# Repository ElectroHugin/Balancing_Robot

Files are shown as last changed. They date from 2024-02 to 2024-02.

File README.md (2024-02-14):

# Balancing_Robot

## Description
Self balancing robot with two wheels. Scope of functionality depends on sensors and is still work in progress.

## Materials
- ESP32 Dev Kit C V4 mit CP2102
- Later on custom board with ESP32-S3-WROOM
- SiliconLabs Uart-to-USB CP2102
- ~~Accelerometer / Gyroscope / Magnetometer BNO085~~
- Accelerometer / Gyroscope MPU6050
- VL53L0X Time-of-Flight (TOF) Laser distance sensor
- (HC-SR04 Ultrasound Module)
- (MAX7219 8x8 1 Dot Matrix MCU LED Display Module)
- ~~BMP180 Barometric Air Pressure and Temperature Sensor~~
- ~~DHT22 Temperature Sensor and Humidity Sensor~~
- ~~Photo LDR Resistor Diodes~~
- ~~L298N H-Bridge Motor Driver~~
- TB6612FNG Motor Driver
- USB-C PD with Battery
- ~~MT3608 DC-DC power supply adapter step up module~~
    ~~- Input voltage: 2V - 24V~~
    ~~- Output voltage: 3V - 28V~~
- ~~OR M2596S Step-down DC-DC Buck Converter~~
    ~~-  Input voltage: 4-40V~~
    ~~-  Output voltage: 3.3-24V~~
- JGA25-371 DC-Motor 12V with Hall-Encoder 65mm wheels

## Visuals
### 3D Model

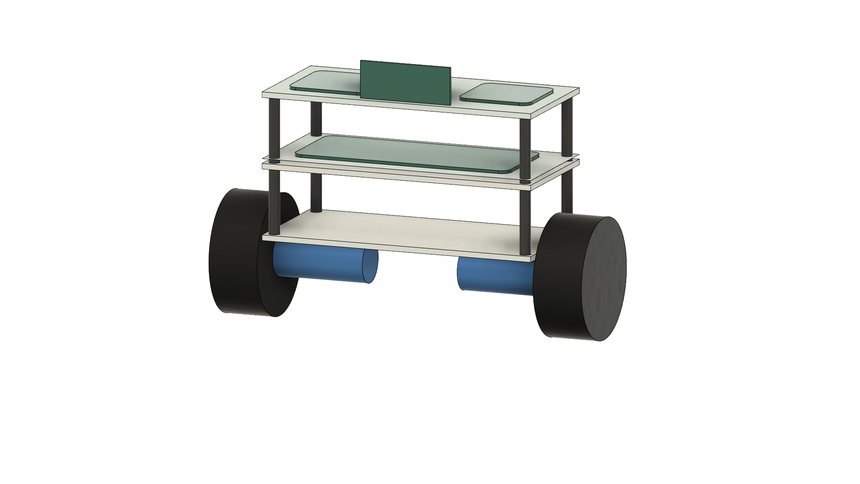
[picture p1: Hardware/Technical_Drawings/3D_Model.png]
Visual representation of 3D Model 3D-Render of Model


### PCB Models
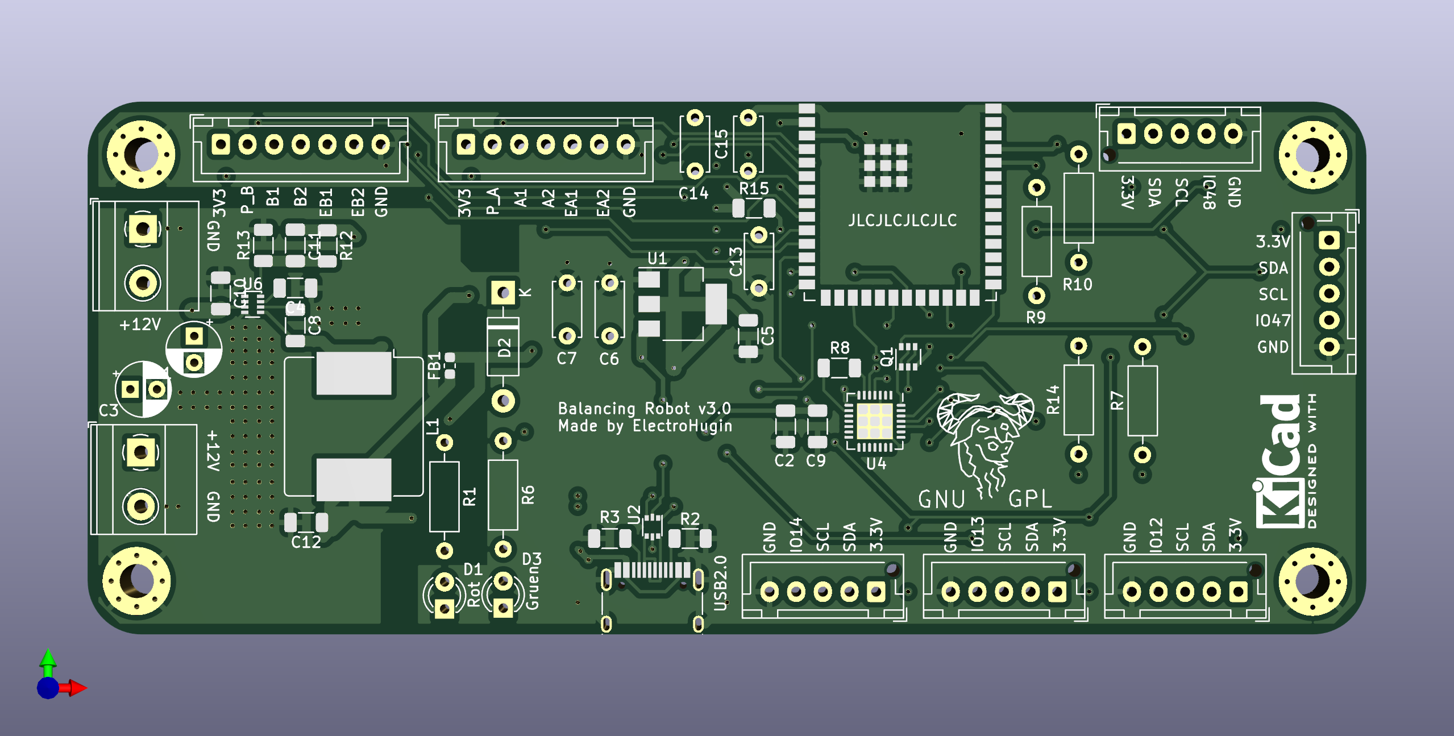
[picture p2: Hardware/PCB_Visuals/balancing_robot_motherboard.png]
Motherboard PCB of Motherboard


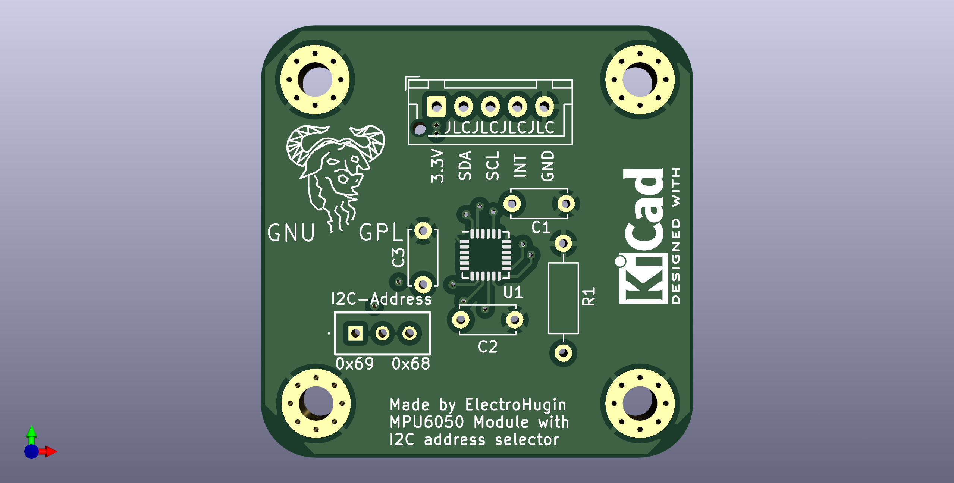
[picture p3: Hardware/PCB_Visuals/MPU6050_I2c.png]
MPU6050 PCB of MPU6050-Board


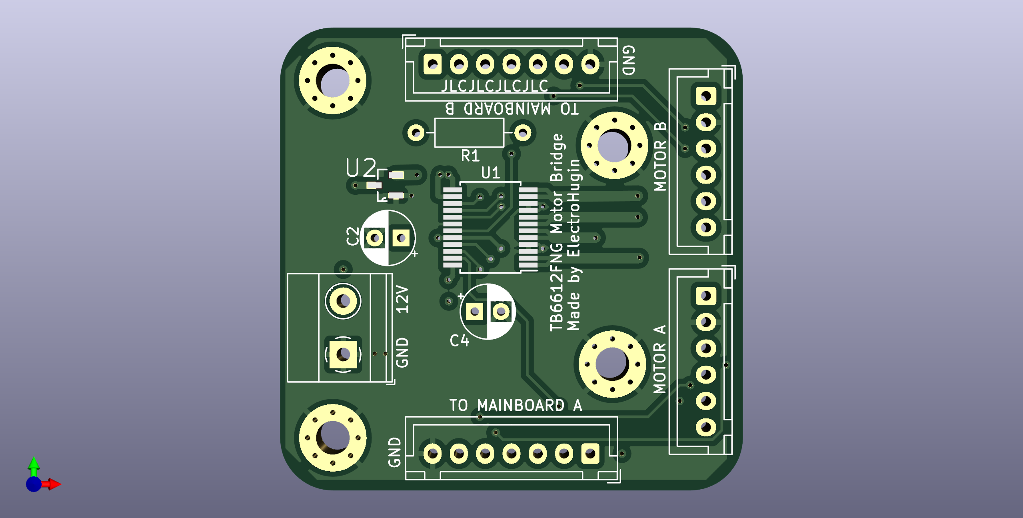
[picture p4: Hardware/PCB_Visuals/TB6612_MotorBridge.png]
Motherboard PCB of TB6612FNG-Board


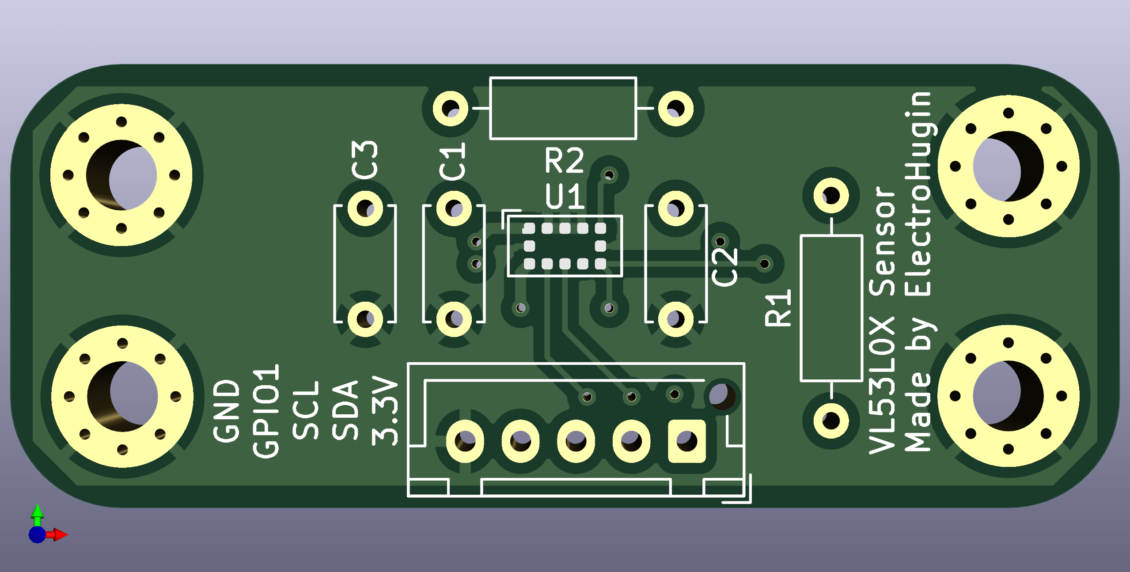
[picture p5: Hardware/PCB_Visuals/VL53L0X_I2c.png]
Motherboard PCB of VL53L0X-Board


## Installation
WIP

## Usage
WIP

## License
Licenses under GNU GENERAL PUBLIC LICENSE Version 3, 29 June 2007

## Project status
Still at the beginning of project.

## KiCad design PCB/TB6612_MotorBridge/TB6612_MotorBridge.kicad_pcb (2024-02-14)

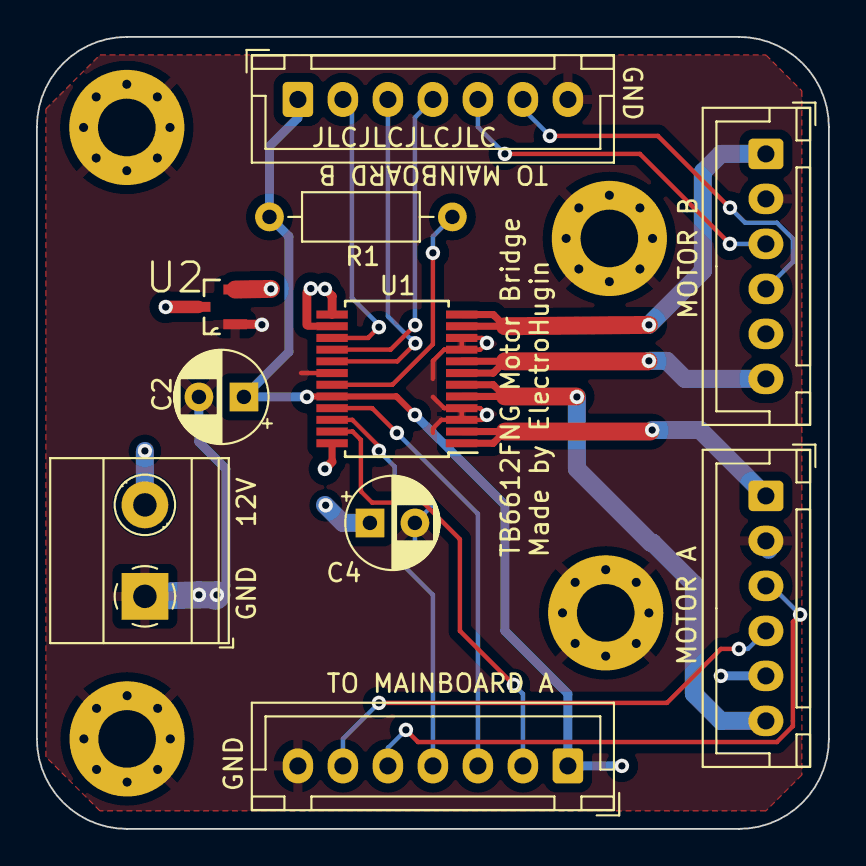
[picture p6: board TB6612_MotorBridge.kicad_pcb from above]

Board: 4 copper layers, 44.0 x 44.0 mm, 14 parts (0 on the bottom side), 19 nets.

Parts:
C2, C4: 10u; CP_Radial_D5.0mm_P2.50mm
H1, H2, H3, H4: Hole_Pad; MountingHole_3.2mm_M3_Pad_Via
J1, J2: Conn_01x07; JST_XH_B7B-XH-A_1x07_P2.50mm_Vertical
J3: Screw_Terminal_01x02; TerminalBlock_Phoenix_MKDS-1,5-2-5.08_1x02_P5.08mm_Horizont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
J4, J5: Conn_01x06; JST_XH_B6B-XH-A_1x06_P2.50mm_Vertical
R1: 10K; R_Axial_DIN0207_L6.3mm_D2.5mm_P10.16mm_Horizontal
U1: TB6612FNG; SSOP-24_5.3x8.2mm_P0.65mm
U2: DMG3415U-7; SOT95P240X105-3N

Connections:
+3.3V: C2.1, J1.1, J2.1, J4.5, J5.5, R1.1, U1.20 (VCC)
+12V: C4.1, U1.13 (VM2), U1.14 (VM3), U1.24 (VM1), U2.2 (S)
/12VA: J3.2, U2.3 (D)
/A1: J1.3, U1.21 (AIN1)
/A2: J1.4, U1.22 (AIN2)
/B1: J2.3, U1.17 (BIN1)
/B2: J2.4, U1.16 (BIN2)
/EA1: J1.5, J4.3
/EA2: J1.6, J4.4
/EB1: J2.5, J5.3
/EB2: J2.6, J5.4
/MA1: J4.1, U1.1 (AO1), U1.2 (AO1)
/MA2: J4.6, U1.5 (AO2), U1.6 (AO2)
/MB1: J5.1, U1.11 (BO1), U1.12 (BO1)
/MB2: J5.6, U1.7 (BO2), U1.8 (BO2)
/PWM_A: J1.2, U1.23 (PWMA)
/PWM_B: J2.2, U1.15 (PWMB)
GND: C2.2, C4.2, H1.1, H2.1, H3.1, H4.1, J1.7, J2.7, J3.1, J4.2, J5.2, U1.3 (PGND1), U1.4 (PGND1), U1.9 (PGND2), U1.10 (PGND2), U1.18 (GND), U2.1 (G)
unnamed: R1.2, U1.19 (STBY)

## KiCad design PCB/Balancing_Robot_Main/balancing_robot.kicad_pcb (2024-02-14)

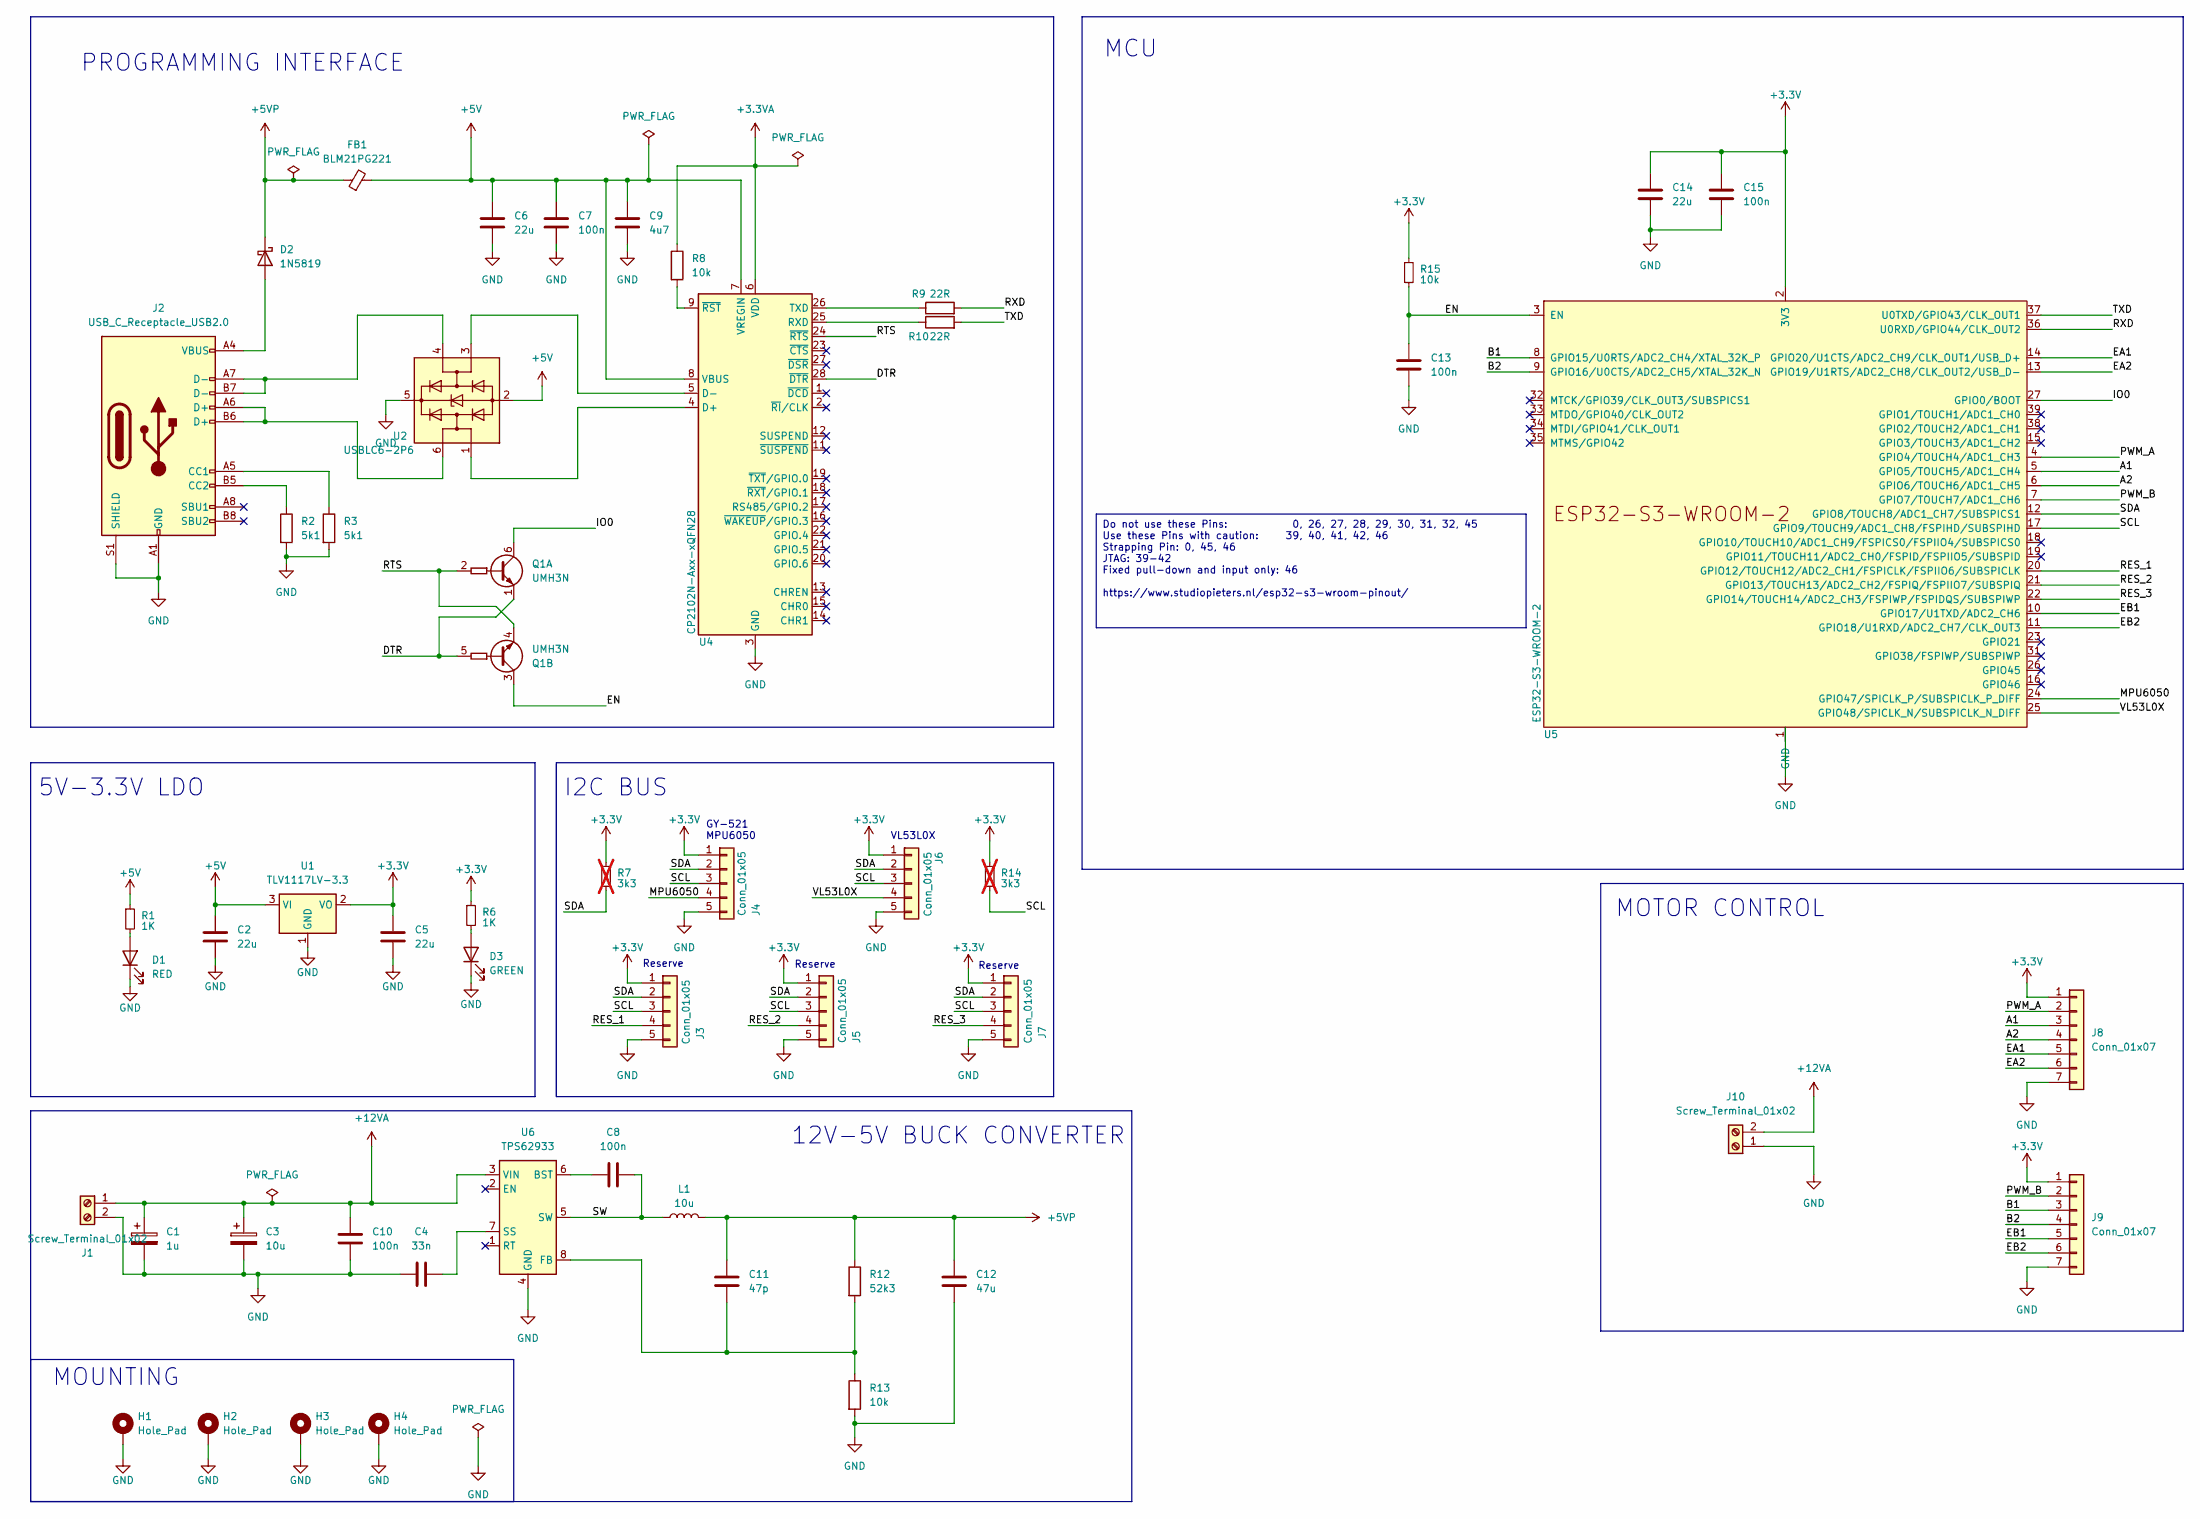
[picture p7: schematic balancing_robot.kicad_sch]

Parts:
C1: 1u; CP_Radial_D5.0mm_P2.50mm
C2, C5: 22u; C_1206_3216Metric
C3: 10u; CP_Radial_D5.0mm_P2.50mm
C4: 33n; C_1206_3216Metric
C6, C14: 22u; C_Disc_D5.0mm_W2.5mm_P5.00mm
C7, C13, C15: 100n; C_Disc_D5.0mm_W2.5mm_P5.00mm
C8, C10: 100n; C_1206_3216Metric
C9: 4u7; C_1206_3216Metric
C11: 47p; C_1206_3216Metric
C12: 47u; C_1206_3216Metric
D1: RED; LED_D3.0mm
D2: 1N5819; D_DO-41_SOD81_P10.16mm_Horizontal
D3: GREEN; LED_D3.0mm
FB1: BLM21PG221; L_0603_1608Metric
H1, H2, H3, H4: Hole_Pad; MountingHole_3.2mm_M3_Pad_Via
J1, J10: Screw_Terminal_01x02; TerminalBlock_Phoenix_MKDS-1,5-2-5.08_1x02_P5.08mm_Horizont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
J2: USB_C_Receptacle_USB2.0; USB_C_Receptacle_HRO_TYPE-C-31-M-12
J3, J4, J5, J6, J7: Conn_01x05; JST_XH_B5B-XH-AM_1x05_P2.50mm_Vertical
J8, J9: Conn_01x07; JST_XH_B7B-XH-A_1x07_P2.50mm_Vertical
L1: 10u; L_Bourns_SRR1208_12.7x12.7mm
Q1: UMH3N; SOT-363_SC-70-6
R1, R6: 1K; R_Axial_DIN0207_L6.3mm_D2.5mm_P10.16mm_Horizontal
R2, R3: 5k1; R_1206_3216Metric
R7, R14: 3k3; R_Axial_DIN0207_L6.3mm_D2.5mm_P10.16mm_Horizontal; not fitted
R8, R13, R15: 10k; R_1206_3216Metric
R9, R10: 22R; R_Axial_DIN0207_L6.3mm_D2.5mm_P10.16mm_Horizontal
R12: 52k3; R_1206_3216Metric
U1: TLV1117LV-3.3; SOT-223-3_TabPin2
U2: USBLC6-2P6; SOT-666
U4: CP2102N-Axx-xQFN28; QFN-28-1EP_5x5mm_P0.5mm_EP3.35x3.35mm
U5: ESP32-S3-WROOM-2
U6: TPS62933; SOT-583-8

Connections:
+3.3V: C5.1, C14.1, C15.1, J3.1, J4.1, J5.1, J6.1, J7.1, J8.1, J9.1, R6.1, R7.1, R14.1, R15.1, U1.2 (VO), U5.2 (3V3)
+3.3VA: R8.1, U4.6 (VDD)
+5V: C2.1, C6.1, C7.1, C9.1, FB1.2, R1.1, U1.3 (VI), U2.2 (GND), U4.7 (VREGIN), U4.8 (VBUS)
+5VP: C11.1, C12.1, D2.1 (K), FB1.1, L1.2, R12.1
+12VA: C1.1, C3.1, C10.2, J1.1, J10.2, U6.3 (VIN)
/A1: J8.3, U5.5 (GPIO5/TOUCH5/ADC1_CH4)
/A2: J8.4, U5.6 (GPIO6/TOUCH6/ADC1_CH5)
/B1: J9.3, U5.8 (GPIO15/U0RTS/ADC2_CH4/XTAL_32K_P)
/B2: J9.4, U5.9 (GPIO16/U0CTS/ADC2_CH5/XTAL_32K_N)
/DTR: Q1.1 (E1), Q1.5 (B2), U4.28 (~DTR)
/EA1: J8.5, U5.14 (GPIO20/U1CTS/ADC2_CH9/CLK_OUT1/USB_D+)
/EA2: J8.6, U5.13 (GPIO19/U1RTS/ADC2_CH8/CLK_OUT2/USB_D-)
/EB1: J9.5, U5.10 (GPIO17/U1TXD/ADC2_CH6)
/EB2: J9.6, U5.11 (GPIO18/U1RXD/ADC2_CH7/CLK_OUT3)
/EN: C13.1, Q1.3 (C2), R15.2, U5.3 (EN)
/IO0: Q1.6 (C1), U5.27 (GPIO0/BOOT)
/MPU6050: J4.4, U5.24 (GPIO47/SPICLK_P/SUBSPICLK_P_DIFF)
/PWM_A: J8.2, U5.4 (GPIO4/TOUCH4/ADC1_CH3)
/PWM_B: J9.2, U5.7 (GPIO7/TOUCH7/ADC1_CH6)
/RES_1: J3.4, U5.20 (GPIO12/TOUCH12/ADC2_CH1/FSPICLK/FSPIIO6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)
/RES_2: J5.4, U5.21 (GPIO13/TOUCH13/ADC2_CH2/FSPIQ/FSPIIO7/S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)
/RES_3: J7.4, U5.22 (GPIO14/TOUCH14/ADC2_CH3/FSPIWP/FSPIDQS/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)
/RTS: Q1.2 (B1), Q1.4 (E2), U4.24 (~RTS)
/RXD: R9.2, U5.36 (U0RXD/GPIO44/CLK_OUT2)
/SCL: J3.3, J4.3, J5.3, J6.3, J7.3, R14.2, U5.17 (GPIO9/TOUCH9/ADC1_CH8/FSPIHD/SUBSPIHD)
/SDA: J3.2, J4.2, J5.2, J6.2, J7.2, R7.2, U5.12 (GPIO8/TOUCH8/ADC1_CH7/SUBSPICS1)
/SW: C8.2, L1.1, U6.5 (SW)
/TXD: R10.2, U5.37 (U0TXD/GPIO43/CLK_OUT1)
/VL53L0X: J6.4, U5.25 (GPIO48/SPICLK_N/SUBSPICLK_N_DIFF)
GND: C1.2, C2.2, C3.2, C4.1, C5.2, C6.2, C7.2, C9.2, C10.1, C12.2, C13.2, C14.2, C15.2, D1.1 (K), D3.1 (K), H1.1, H2.1, H3.1, H4.1, J1.2, J2.A1 (GND), J2.A12 (GND), J2.B1 (GND), J2.B12 (GND), J2.S1 (SHIELD), J3.5, J4.5, J5.5, J6.5, J7.5, J8.7, J9.7, J10.1, R2.2, R3.2, R13.2, U1.1 (GND), U2.5 (VBUS), U4.3 (GND), U4.29 (GND), U5.1 (GND), U5.40 (GND), U5.41 (GND), U6.4 (GND)
unnamed: D1.2 (A), R1.2
unnamed: D2.2 (A), J2.A4 (VBUS), J2.A9 (VBUS), J2.B4 (VBUS), J2.B9 (VBUS)
unnamed: D3.2 (A), R6.2
unnamed: J2.A5 (CC1), R3.1
unnamed: J2.B5 (CC2), R2.1
unnamed: J2.A6 (D+), J2.B6 (D+), U2.6 (I/O1)
unnamed: J2.A7 (D-), J2.B7 (D-), U2.4 (I/O2)
unnamed: U2.1 (I/O1), U4.4 (D+)
unnamed: U2.3 (I/O2), U4.5 (D-)
unnamed: R10.1, U4.25 (RXD)
unnamed: R9.1, U4.26 (TXD)
unnamed: R8.2, U4.9 (~RST)
unnamed: C8.1, U6.6 (BST)
unnamed: C11.2, R12.2, R13.1, U6.8 (FB)
unnamed: C4.2, U6.7 (SS)

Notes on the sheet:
Do not use these Pins: 0, 26, 27, 28, 29, 30, 31, 32, 45 Use these Pins with caution: 39, 40, 41, 42, 46 Strapping Pin: 0, 45, 46 JTAG: 39-42 Fixed pull-down and input only: 46 https://www.studiopieters.nl/esp32-s3-wroom-pinout/
I2C BUS
GY-521 MPU6050
MCU
Reserve
VL53L0X
MOUNTING
12V-5V BUCK CONVERTER
5V-3.3V LDO
PROGRAMMING INTERFACE
MOTOR CONTROL

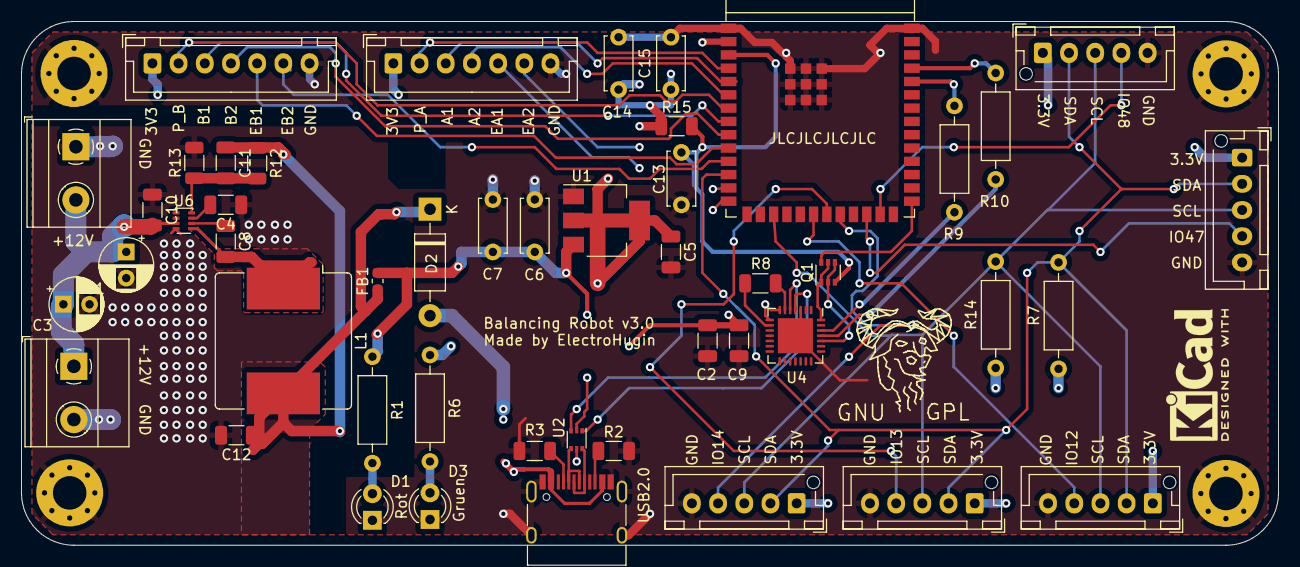
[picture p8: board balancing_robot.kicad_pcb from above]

Board: 4 copper layers, 120.0 x 50.0 mm, 52 parts (0 on the bottom side), 45 nets.

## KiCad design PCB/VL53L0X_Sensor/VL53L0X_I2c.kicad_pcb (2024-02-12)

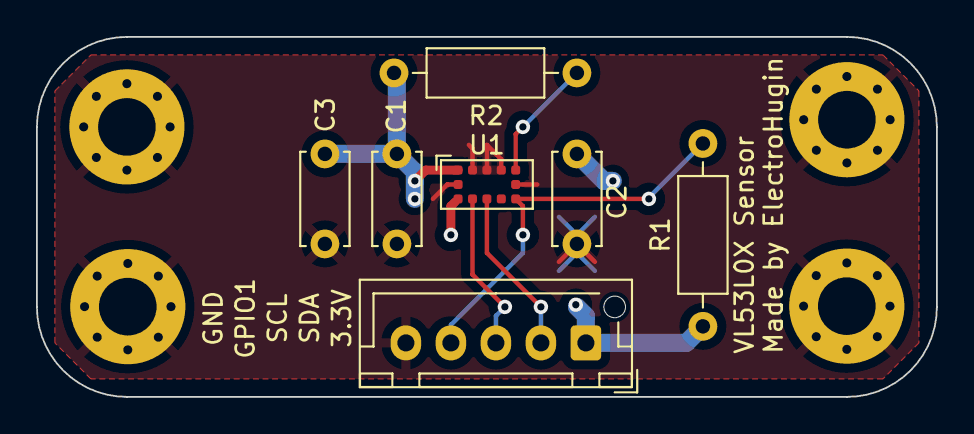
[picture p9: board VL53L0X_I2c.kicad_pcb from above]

Board: 4 copper layers, 50.0 x 20.0 mm, 11 parts (0 on the bottom side), 6 nets.

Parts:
C1: 0.1u; C_Disc_D5.0mm_W2.5mm_P5.00mm
C2: 4.7u; C_Disc_D5.0mm_W2.5mm_P5.00mm
C3: 1u; C_Disc_D5.0mm_W2.5mm_P5.00mm
H1, H2, H3, H4: Hole_Pad; MountingHole_3.2mm_M3_Pad_Via
J1: Conn_01x05; JST_XH_B5B-XH-AM_1x05_P2.50mm_Vertical
R1, R2: 47k; R_Axial_DIN0207_L6.3mm_D2.5mm_P10.16mm_Horizontal
U1: VL53L1CXV0FY1; ST_VL53L1x

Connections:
+3.3V: C1.1, C2.1, C3.1, J1.1, R1.1, R2.1, U1.1 (AVDDVCSEL), U1.11 (AVDD)
/SCL: J1.3, U1.10 (SCL)
/SDA: J1.2, U1.9 (SDA)
/VL53L0X: J1.4, R1.2, U1.7 (GPIO1)
GND: C1.2, C2.2, C3.2, H1.1, H2.1, H3.1, H4.1, J1.5, U1.2 (AVSSVCSEL), U1.3 (GND), U1.4 (GND), U1.6 (GND), U1.12 (GND)
unnamed: R2.2, U1.5 (XSHUT)

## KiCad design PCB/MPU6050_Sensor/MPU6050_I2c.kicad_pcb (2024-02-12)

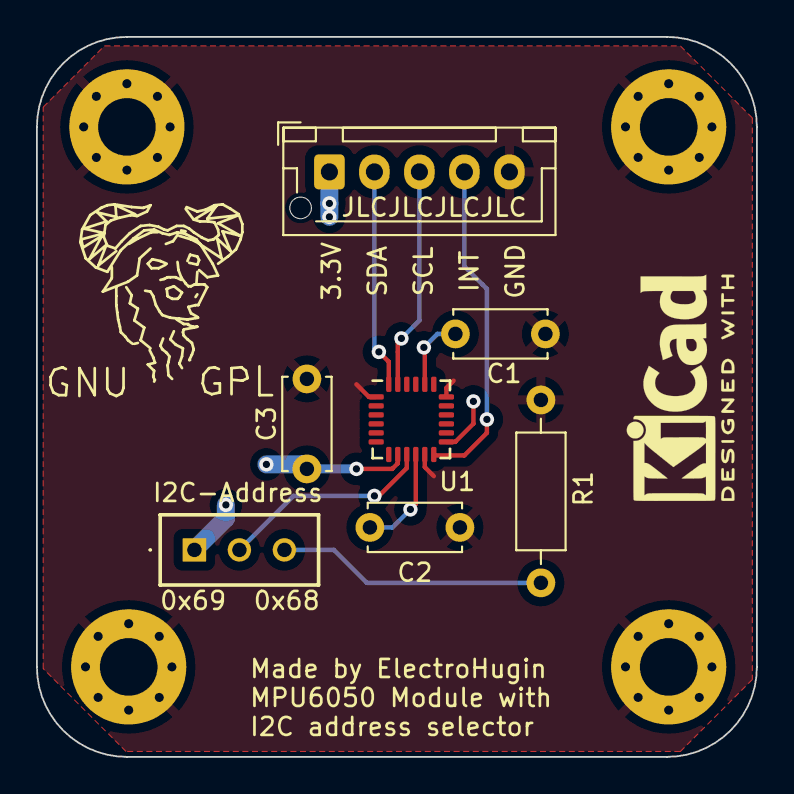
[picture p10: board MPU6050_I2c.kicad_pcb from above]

Board: 4 copper layers, 40.0 x 40.0 mm, 11 parts (0 on the bottom side), 9 nets.

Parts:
C1: 2200p; C_Disc_D5.0mm_W2.5mm_P5.00mm
C2, C3: 0.1u; C_Disc_D5.0mm_W2.5mm_P5.00mm
H1, H2, H3, H4: Hole_Pad; MountingHole_3.2mm_M3_Pad_Via
J1: Conn_01x05; JST_XH_B5B-XH-AM_1x05_P2.50mm_Vertical
R1: 4k7; R_Axial_DIN0207_L6.3mm_D2.5mm_P10.16mm_Horizontal
SW1: SW_SPDT; SLW8839352AD
U1: MPU-6050; InvenSense_QFN-24_4x4mm_P0.5mm

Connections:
+3.3V: C3.2, J1.1, SW1.1 (A), U1.8 (VLOGIC), U1.13 (VDD)
/MPU6050: J1.4, U1.12 (INT)
/SCL: J1.3, U1.23 (SCL)
/SDA: J1.2, U1.24 (SDA)
GND: C1.2, C2.1, C3.1, H1.1, H2.1, H3.1, H4.1, J1.5, R1.2, U1.1 (CLKIN), U1.11 (FSYNC), U1.18 (GND)
unnamed: SW1.2 (B), U1.9 (AD0)
unnamed: R1.1, SW1.3 (C)
unnamed: C1.1, U1.20 (CPOUT)
unnamed: C2.2, U1.10 (REGOUT)

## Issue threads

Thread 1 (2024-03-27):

Integrate USB-C PD in main PCB as second USB-C connector

ElectroHugin, 2024-03-27:
Power delivery is currently built in with a USB-C PD breakout board. A USB-C PD chip can be added with an additional USB-C connector to pull 12V, 15V or 20V from an attached USB-C powerbank.

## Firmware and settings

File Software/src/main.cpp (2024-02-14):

#include <Arduino.h>
#include <Wire.h>
#include "ToFLib.h"
#include "MPU6050EH.h"
#include "DriveLib.h"

#define DELAY 100

MPU6050EH mpuEH;
VL53L0XEH tofEH;
JGA25_371 motor;

u_int16_t tof_distance;
u_long imu_timestamp;
u_long current_time;

void setup() {
  Wire.begin();
  Wire.setClock(400000);

   Serial.begin(115200);

    while (!Serial) {
        delay(1);
    }

    Serial.println(F("Initializing I2C devices..."));

    if (tofEH.init()) {
        Serial.println("VL53L0X Found!");
    } else {
        Serial.println("Failed to find VL53L0X sensor");
    }

    if(mpuEH.init()) {
      Serial.println("MPU6050 Found!");
    } else {
      Serial.println("Failed to find MPU6050 sensor");
    }

    if(motor.init()) {
      Serial.println("Motor 1 initialized!");
    } else {
      Serial.println("Failed to initialize Motor 1");
    }
  current_time = millis();
}

void loop() {
  //imu_timestamp = micros();
  
  if (millis() - current_time > DELAY) {
    current_time = millis();

    //Serial.print("rhCount: ");
    //Serial.println(motor_1.getRhCount());
    Serial.print("RH Turns: ");
    Serial.println(motor.getRHturns());
    //Serial.print("lhCount: ");
    //Serial.println(motor_1.getLhCount());
    Serial.print("LH Turns: ");
    Serial.println(motor.getLHturns());

    /*if (tofEH.measure()) {
      tof_distance = tofEH.getRangeMilliMeter();
      Serial.print("Distance: ");
      Serial.print(tof_distance);
      Serial.println(" mm");
    } else {
      Serial.println("Failed to measure distance");
    }

    if (mpuEH.accelgyroData()) {
      Serial.print("Yaw: ");
      Serial.println(mpuEH.yaw());

      Serial.print("Pitch: ");
      Serial.println(mpuEH.pitch());

      Serial.print("Roll: ");
      Serial.println(mpuEH.roll());

      Serial.print("AccelX: ");
      Serial.println(mpuEH.getAccelX());

      Serial.print("AccelY: ");
      Serial.println(mpuEH.getAccelY());

      Serial.print("AccelZ: ");
      Serial.println(mpuEH.getAccelZ());
    } else {
      Serial.println("Failed to get IMU data");
    }

  */
  }
}

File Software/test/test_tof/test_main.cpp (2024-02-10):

#include <unity.h>
#include "ToFLib.h"
#include <Arduino.h>
#include <Wire.h>

void setUp(void)
{
    Wire.begin();
    Wire.setClock(400000);
}

void tearDown(void)
{
    // clean stuff up here
}

void test_VL53L0XEH()
{
    // Create an instance of the ToFLib class
    VL53L0XEH ToF;

    // Perform distance measurement
    TEST_ASSERT_TRUE(ToF.init());
    TEST_ASSERT_TRUE(ToF.measure());

    // Assert that the measured distance is within a valid range
    TEST_ASSERT_INT16_WITHIN(500, 0, ToF.getRangeMilliMeter());
}

void setup()
{
    delay(2000);

    Wire.begin();
    Wire.setClock(400000);
    
    UNITY_BEGIN();
    RUN_TEST(test_VL53L0XEH);
    UNITY_END();
}

void loop() {
    // loop stuff here
}

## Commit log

2024-01-27 Added Materials
2024-01-27 Added Sensors and Actuators
2024-01-28 Added Info about wheels and motor
2024-02-02 Added KiCad Schematic and some Datasheets
    [ESP32-S3-WROOM-1 PCB Footprint.dxf, ESP32-S3-WROOM-2 PCB Footprint.dxf, balancing_robot.kicad_pcb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]
2024-02-02 Added BNO_0xx datasheet and schematic
    [balancing_robot.kicad_sch]
2024-02-03 Added Datasheet motor and model drawing
2024-02-05 Added BNO Imu functionality
2024-02-08 Added Board Schematic and PCB and Code for MPU6050
    [HRO TYPE-C-31-M-12.step, HRO_TYPE-C-31-M-12.step, JST - XH - Thru - 5Pin - 2.5mm (Genuine).stp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]
2024-02-09 Added Sensor PCBs and experimented with MPU code
    [ESP32-S3-WROOM-1 PCB Footprint.dxf, ESP32-S3-WROOM-2 PCB Footprint.dxf, HRO TYPE-C-31-M-12.step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]
2024-02-10 Working Version of MPU6050 Library
    [MPU6050_I2c.kicad_pcb]
2024-02-10 Working Version of ToFLib finished, cm and m still bugged
    [main.cpp, test_main.cpp]
2024-02-10 Added Encoder counter for motor
2024-02-11 Restructured folders
    [MPU6050_I2c.kicad_pcb, MPU6050_I2c.kicad_sch, VL53L0X_I2c.kicad_pcb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]
2024-02-11 Added Motor Bridge based on TB6612FNG
    [TB6612_MotorBridge.kicad_pcb, TB6612_MotorBridge.kicad_sch]
2024-02-12 Updated PCB Main and MotorBridge with Pins for Encoder
    [TB6612_MotorBridge.kicad_pcb, TB6612_MotorBridge.kicad_sch, balancing_robot.kicad_pcb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]
2024-02-12 Converted all vias to through-hole
    [MPU6050_I2c.kicad_pcb, TB6612_MotorBridge.kicad_pcb, VL53L0X_I2c.kicad_pcb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]
2024-02-14 Added Visuals
    [TB6612_MotorBridge.kicad_pcb, balancing_robot.kicad_pcb, balancing_robot.kicad_sch]
2024-02-14 Added Connectivity to second Motor LH
